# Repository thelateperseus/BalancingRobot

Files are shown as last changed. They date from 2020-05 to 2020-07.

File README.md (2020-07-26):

Balancing Robot Project
=======================

An Arduino-based, two-wheeled balancing robot.

Components:
* Arduino Nano
* MPU-6050 6 DoF sensor
* L298N motor driver
* Machifit 25GA370 DC 12V 130rpm Gear Reduction Motor with Mounting Bracket and Wheel
* 2x 4-AA battery holders with switch
* HC-06 bluetooth module for remote control (via Android app or hand-held remote control)

Control Algorithm
-----------------

The main control alorithm changes the motor speed based on the measured angle. If the robot tips forward or backward, the motors drive forward or backward to prevent the robot from falling over. Two PID controllers are used to achieve this. The first measures the angle from the MPU-6050 and changes the motor speed PWM signal. The second uses the motor speed PWM signal and changes the angle set point. The remote control sets the speed set point, and the PID controller adjusts the angle set point accordingly.

```
              Speed             Speed                   Angle             Angle                  Speed              Angle
-----------  setpoint  -------  error  --------------  setpoint  -------  error  --------------  output  ---------  reading
| Remote  | ---------> | Sum | ------> | Speed PID  | ---------> | Sum | ------> | Angle PID  | ---+---> | Robot | ---
| Control |          + -------         | Controller |          + -------         | Controller |    |     ---------   |
-----------               ^  -         --------------               ^  -         --------------    |                 |
                          |                                         |                              |                 |
                          |                                         -------------------------------+------------------
                          |                                                                        |
                          --------------------------------------------------------------------------
```

The motors do not have encoders, so the speed PWM signal is used as the actual speed of the robot. If the motors had encoders, we would read the actual speed from the encoders instead.

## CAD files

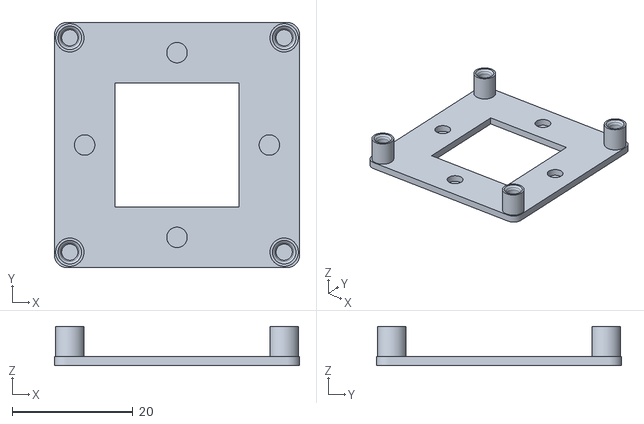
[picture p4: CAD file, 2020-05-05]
Solarbotics_L298_Compact_Motor_Driver_Mounting_Plate.stl
40.6 x 40.6 x 6.50

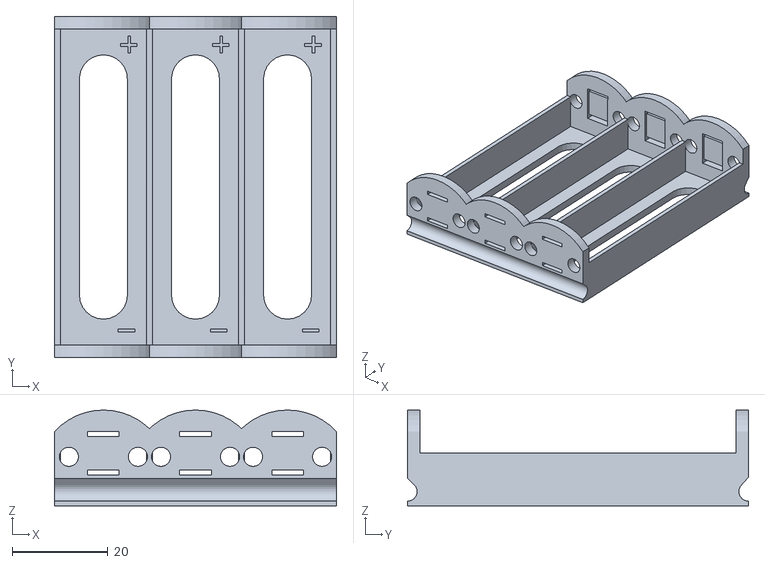
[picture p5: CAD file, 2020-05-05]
battaryholder3.stl
58.8 x 71.1 x 20.0

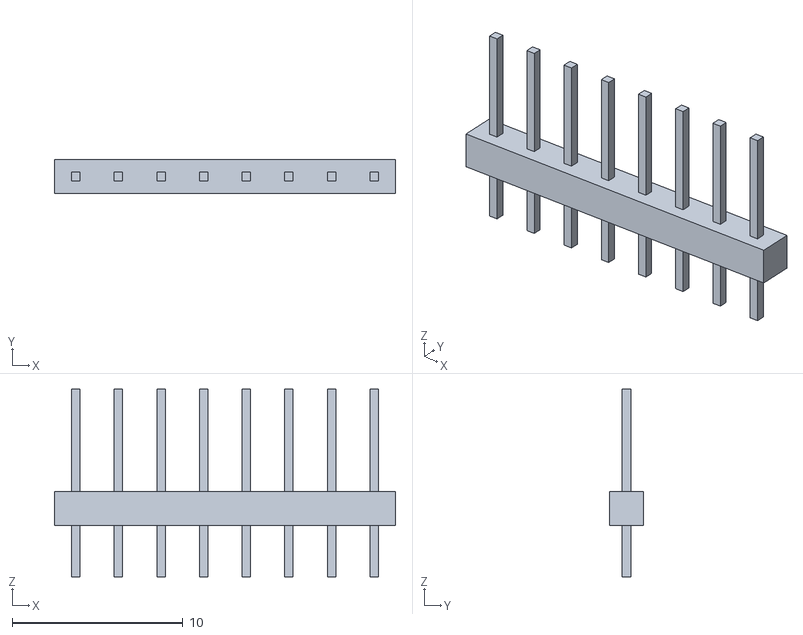
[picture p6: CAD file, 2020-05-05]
gy521_pins.stl
20.0 x 2.00 x 11.0

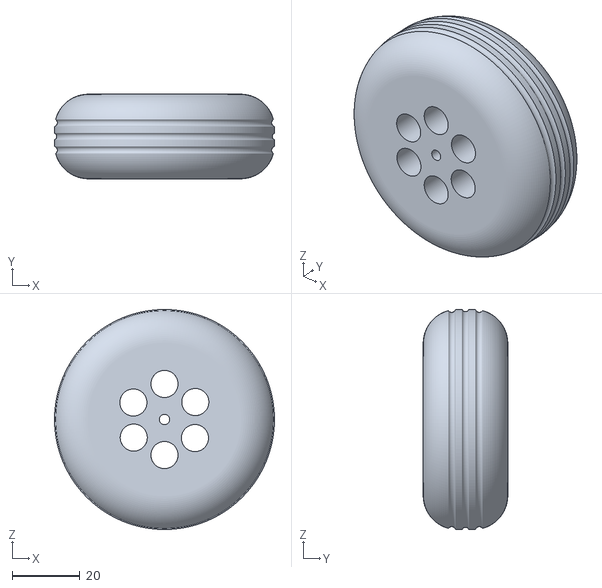
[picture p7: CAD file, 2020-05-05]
Wheel_65mm.stl
65.0 x 25.0 x 65.0

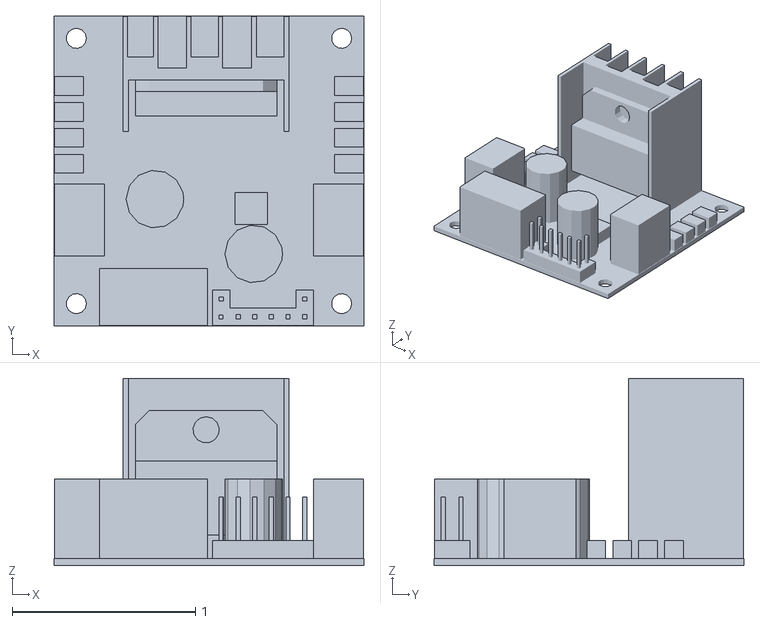
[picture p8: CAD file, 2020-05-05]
motor_driver.stl
1.69 x 1.69 x 1.02

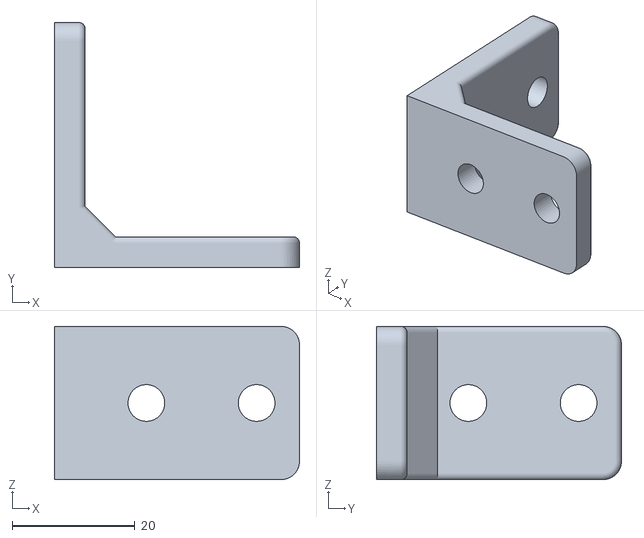
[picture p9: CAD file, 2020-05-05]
CornerBracket.stl
40.0 x 40.0 x 25.0

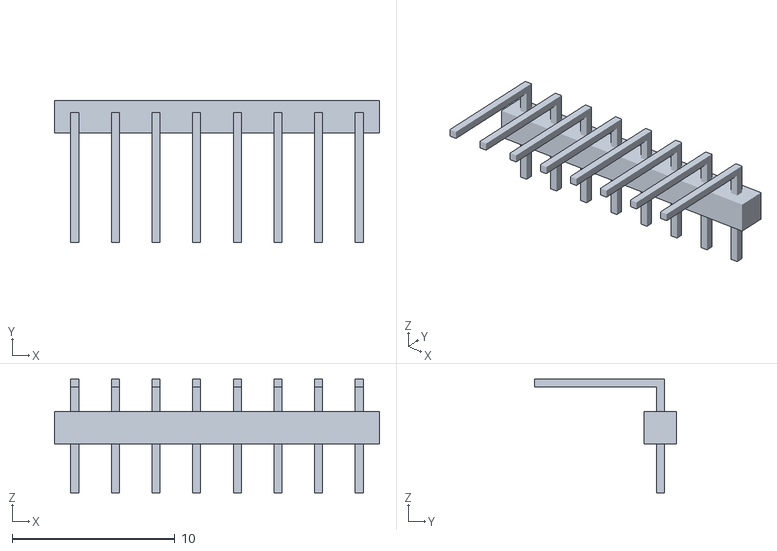
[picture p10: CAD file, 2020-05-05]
gy521_pins90deg.stl
20.0 x 8.75 x 7.00

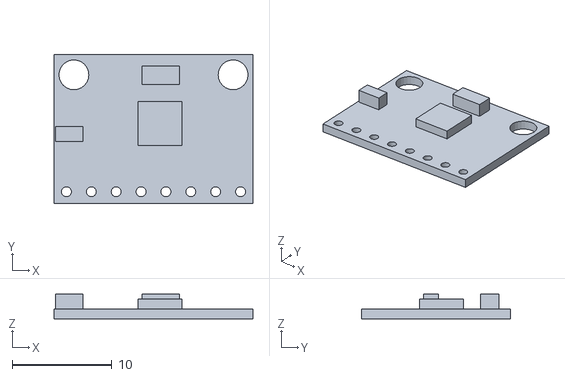
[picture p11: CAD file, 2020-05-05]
GY-521_MPU-6050.stl
20.0 x 15.0 x 2.50

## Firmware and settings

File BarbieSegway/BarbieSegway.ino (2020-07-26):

#include <Wire.h>
#include <PID_v1.h>
#include <SoftwareSerial.h>

const int IN1 = 7;
const int IN2 = 8;
const int ENA = 6;
const int IN3 = 9;
const int IN4 = 10;
const int ENB = 11;

const int GYRO_ADDRESS = 0x68;
const int ACCELEROMETER_Z_CALIBRATION = 300;
const int LOOP_MICROS = 4000;

boolean started = false;

long gyroXCalibration = 0, gyroYCalibration = 0;

double pitchSetPoint = 0;
double pitchReading = 0;
double pitchPidOutput = 0;
PID pitchPid(&pitchReading, &pitchPidOutput, &pitchSetPoint, 40, 140, 1, REVERSE);

double speedSetPoint = 0;
double filteredSpeed = 0;
double speedPidOutput = 0;
//PID speedPid(&pitchPidOutput, &speedPidOutput, &speedSetPoint, 0.00025, 0, 0.000005, DIRECT);
PID speedPid(&filteredSpeed, &speedPidOutput, &speedSetPoint, 0.00000008, 0.02 , 0, DIRECT);

double yawSetPoint = 0;
double yawReading = 0;
double yawOutput = 0;
PID yawPid(&yawReading, &yawOutput, &yawSetPoint, 1.5, 0, 0, DIRECT);

int activeCommand = -1;
unsigned long commandTimer = 0;

unsigned long loopEndTime = 0;

SoftwareSerial BTSerial(2, 3); // RX | TX

//Low pass butterworth filter order=1 alpha1=0.04
//http://www.schwietering.com/jayduino/filtuino/index.php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
class  LowPassFilter
{
  public:
    LowPassFilter() {
      v[0] = 0.0;
    }
  private:
    double v[2];
  public:
    double step(double x) { //class II
      v[0] = v[1];
      // 20Hz
      //v[1] = (2.043008243002644164e-1 * x)
      //   + (0.59139835139947116716 * v[0]);
      // 10Hz
      v[1] = (1.121602444751934047e-1 * x)
             + (0.77567951104961319064 * v[0]);
      return v[0] + v[1];
    }
};

LowPassFilter speedFilter = LowPassFilter();

void setup() {
  Serial.begin(115200);
  BTSerial.begin(38400);
  Serial.println("Initializing MPU-6050...");

  // Wake up the MPU-6050
  Wire.beginTransmission(GYRO_ADDRESS);
  Wire.write(0x6B); // PWR_MGMT_1 register
  Wire.write(0x00);
  Wire.endTransmission();
  // Set the full scale of the gyro to +/- 250 degrees per second
  Wire.beginTransmission(GYRO_ADDRESS);
  Wire.write(0x1B); // GYRO_CONFIG register
  Wire.write(0x00);                                                         //Set the register bits as 00000000 (250dps full scale)
  Wire.endTransmission();                                                   //End the transmission with the gyro
  // Set the full scale of the accelerometer to +/- 4g.
  Wire.beginTransmission(GYRO_ADDRESS);
  Wire.write(0x1C); // ACCEL_CONFIG register
  Wire.write(0x08);
  Wire.endTransmission();
  // Enable Digital Low Pass Filter to improve the raw data.
  Wire.beginTransmission(GYRO_ADDRESS);
  Wire.write(0x1A); // CONFIG register
  Wire.write(0x03); // ~43Hz
  Wire.endTransmission();

  Serial.println("Initializing L298N...");

  pinMode(IN1, OUTPUT);
  pinMode(IN2, OUTPUT);
  pinMode(ENA, OUTPUT);
  pinMode(IN3, OUTPUT);
  pinMode(IN4, OUTPUT);
  pinMode(ENB, OUTPUT);

  pitchPid.SetSampleTime(4);
  pitchPid.SetOutputLimits(-255, 255);
  speedPid.SetSampleTime(4);
  speedPid.SetOutputLimits(-15, 15);
  yawPid.SetSampleTime(4);
  yawPid.SetOutputLimits(-15, 15);

  Serial.println("Measuring gyro calibration values...");
  loopEndTime = micros() + LOOP_MICROS;
  for (int i = 0; i < 500; i++) {
    if (i % 15 == 0) {
      digitalWrite(LED_BUILTIN, !digitalRead(LED_BUILTIN));        //Change the state of the LED every 15 loops to make the LED blink fast
    }
    Wire.beginTransmission(GYRO_ADDRESS);
    Wire.write(0x43); // GYRO_XOUT[15:8]
    Wire.endTransmission();
    Wire.requestFrom(GYRO_ADDRESS, 4); // GYRO_XOUT[15:8], GYRO_XOUT[7:0], GYRO_YOUT[15:8], GYRO_YOUT[7:0]
    gyroXCalibration += Wire.read() << 8 | Wire.read();
    gyroYCalibration += Wire.read() << 8 | Wire.read();
    delayMicroseconds(loopEndTime - micros()); // Simulate the main program loop time
    loopEndTime = micros() + LOOP_MICROS;
  }
  // Get the average from the 500 readings
  gyroXCalibration /= 500;
  gyroYCalibration /= 500;

  /*Serial.print("Gyro calibration complete. x: ");
    Serial.print(gyroXCalibration);
    Serial.print(", y: ");
    Serial.println(gyroYCalibration);*/

  // x: -552, y: 66

  Serial.println("Ready to roll!");
  digitalWrite(LED_BUILTIN, HIGH);
  loopEndTime = micros() + LOOP_MICROS;
}

void loop() {
  // Remote control
  // --------------
  int command = -1;
  while (Serial.available()) {
    command = Serial.read(); //reads serial input
  }
  while (BTSerial.available()) {
    command = BTSerial.read(); //reads bluetooth input
  }
  if (command == 'l' || command == 'L') {
    yawSetPoint -= 2;
  } else if (command == 'r' || command == 'R') {
    yawSetPoint += 2;
  } else if (command == 'f' || command == 'F') {
    activeCommand = command;
    commandTimer = millis();
    speedSetPoint = 30;
  } else if (command == 'b' || command == 'B') {
    activeCommand = command;
    commandTimer = millis();
    speedSetPoint = -30;
  }

  unsigned long commandTimeMillis = millis() - commandTimer;
  if (commandTimer > 0 && commandTimeMillis > 150) {
    activeCommand = -1;
    commandTimer = 0;
    speedSetPoint = 0;
  }

  // Angle calculations
  // ------------------
  /* http://www.geekmomprojects.com/gyroscopes-and-accelerometers-on-a-chip/
     Filtered Angle = α × (Gyroscope Angle) + (1 − α) × (Accelerometer Angle)
     where
         α = τ/(τ + Δt)
         (Gyroscope Angle) = (Last Measured Filtered Angle) + ω×Δt
         Δt = sampling rate (4ms)
         τ = time constant greater than timescale of typical accelerometer noise (1s)
  */

  // Read z accelerometer value
  Wire.beginTransmission(GYRO_ADDRESS);
  Wire.write(0x3F); // ACCEL_ZOUT[15:8]
  Wire.endTransmission();
  Wire.requestFrom(GYRO_ADDRESS, 2); // ACCEL_ZOUT[15:8], ACCEL_ZOUT[7:0]
  long accelerometerZ = Wire.read() << 8 | Wire.read();
  accelerometerZ += ACCELEROMETER_Z_CALIBRATION;
  accelerometerZ = constrain(accelerometerZ, -8200, 8200);

  // Calculate the current pitch angle in degrees according to the accelerometer
  float pitchAccelerometer = asin((float)accelerometerZ / 8200.0) * 57.296;

  // Start balancing when angle is close to zero
  if (!started && pitchAccelerometer > -0.5 && pitchAccelerometer < 0.5) {
    pitchReading = pitchAccelerometer;
    started = true;
    pitchPid.SetMode(AUTOMATIC);
    speedPid.SetMode(AUTOMATIC);
    yawPid.SetMode(AUTOMATIC);
  }

  // Read X and Y gyro values
  Wire.beginTransmission(GYRO_ADDRESS);
  Wire.write(0x43); // GYRO_XOUT[15:8]
  Wire.endTransmission();
  Wire.requestFrom(GYRO_ADDRESS, 4); // GYRO_XOUT[15:8], GYRO_XOUT[7:0], GYRO_YOUT[15:8], GYRO_YOUT[7:0]
  long gyroX = Wire.read() << 8 | Wire.read();
  long gyroY = Wire.read() << 8 | Wire.read();

  gyroX -= gyroXCalibration;
  gyroY -= gyroYCalibration;

  // Calculate the angle in degrees traveled during this loop angle
  // (Gyroscope Angle) = (Last Measured Filtered Angle) + ω×Δt
  float pitchGyro = pitchReading + gyroY * 0.000031;

  // Complementary filter to combine the gyro and accelerometer angle
  // Filtered Angle = α × (Gyroscope Angle) + (1 − α) × (Accelerometer Angle)
  pitchReading = pitchGyro * 0.9996 + pitchAccelerometer * 0.0004;

  yawReading -= gyroX * 0.000031;

  if (started) {
    pitchSetPoint = speedPidOutput + 1; // imperfect placement of MPU6050
    pitchPid.Compute();

    //filteredSpeed = speedFilter.step(pitchPidOutput);
    filteredSpeed = pitchPidOutput;
    speedPid.Compute();

    yawPid.Compute();

    //Serial.print("yaw:");
    //Serial.print(yawReading);

    /*Serial.print("psp:");
      Serial.print(pitchSetPoint);
      Serial.print(", p:");
      Serial.print(pitchReading);*/
    Serial.print(", ssp:");
    Serial.print(speedSetPoint);
    Serial.print(", s:");
    Serial.print(pitchPidOutput);
    Serial.print(", fs:");
    Serial.print(filteredSpeed);
    Serial.println();

    /*
      // Deadband to prevent oscillations
      if (pitchPidOutput > 0 && pitchPidOutput < 2) {
      pitchPidOutput = 0;
      }
      if (pitchPidOutput < 0 && pitchPidOutput > -2) {
      pitchPidOutput = 0;
      }
    */

    double speedA = pitchPidOutput + yawOutput;
    double speedB = pitchPidOutput - yawOutput;
    if (pitchReading > 45 || pitchReading < -45 || pitchAccelerometer > 45 || pitchAccelerometer < -45) {
      speedA = 0;
      speedB = 0;
      pitchReading = 0;
      yawReading = 0;
      pitchSetPoint = 0;
      speedSetPoint = 0;
      yawSetPoint = 0;
      pitchPidOutput = 0;
      filteredSpeed = 0;
      speedPidOutput = 0;
      yawOutput = 0;
      activeCommand = -1;
      started = false;
      pitchPid.SetMode(MANUAL);
      speedPid.SetMode(MANUAL);
      yawPid.SetMode(MANUAL);
    }

    speedA = constrain(speedA, -255, 255);
    speedB = constrain(speedB, -255, 255);

    // control speed, deadzone A:50, B:40
    double pwmA = map(abs(speedA), 1, 255, 54, 255);
    double pwmB = map(abs(speedB), 1, 255, 40, 255);
    analogWrite(ENA, pwmA);
    analogWrite(ENB, pwmB);
    //control direction
    digitalWrite(IN1, speedA < 0 ? HIGH : LOW);
    digitalWrite(IN2, speedA > 0 ? HIGH : LOW);
    //direction reversed for second motor (wiring)
    digitalWrite(IN3, speedB < 0 ? LOW : HIGH);
    digitalWrite(IN4, speedB > 0 ? LOW : HIGH);
  }

  // The angle calculations are tuned for a loop time of 4 milliseconds
  delayMicroseconds(loopEndTime - micros()); // Simulate the main program loop time
  loopEndTime = micros() + LOOP_MICROS;
}

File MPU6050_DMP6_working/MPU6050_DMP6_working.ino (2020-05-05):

// I2C device class (I2Cdev) demonstration Arduino sketch for MPU6050 class using DMP (MotionApps v2.0)
// 6/21/2012 by Jeff Rowberg <jeff@rowberg.net>
// Updates should (hopefully) always be available at https://github.com/jrowberg/i2cdevlib
//
// Changelog:
//      2019-07-08 - Added Auto Calibration and offset generator
//		   - and altered FIFO retrieval sequence to avoid using blocking code
//      2016-04-18 - Eliminated a potential infinite loop
//      2013-05-08 - added seamless Fastwire support
//                 - added note about gyro calibration
//      2012-06-21 - added note about Arduino 1.0.1 + Leonardo compatibility error
//      2012-06-20 - improved FIFO overflow handling and simplified read process
//      2012-06-19 - completely rearranged DMP initialization code and simplification
//      2012-06-13 - pull gyro and accel data from FIFO packet instead of reading directly
//      2012-06-09 - fix broken FIFO read sequence and change interrupt detection to RISING
//      2012-06-05 - add gravity-compensated initial reference frame acceleration output
//                 - add 3D math helper file to DMP6 example sketch
//                 - add Euler output and Yaw/Pitch/Roll output formats
//      2012-06-04 - remove accel offset clearing for better results (thanks Sungon Lee)
//      2012-06-01 - fixed gyro sensitivity to be 2000 deg/sec instead of 250
//      2012-05-30 - basic DMP initialization working

/* ============================================
I2Cdev device library code is placed under the MIT license
Copyright (c) 2012 Jeff Rowberg

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
THE SOFTWARE IS PROVIDED "AS IS", WITHOUT WARRANTY OF ANY KIND, EXPRESS OR
IMPLIED, INCLUDING BUT NOT LIMITED TO THE WARRANTIES OF MERCHANTABILITY,
FITNESS FOR A PARTICULAR PURPOSE AND NONINFRINGEMENT. IN NO EVENT SHALL THE
AUTHORS OR COPYRIGHT HOLDERS BE LIABLE FOR ANY CLAIM, DAMAGES OR OTHER
LIABILITY, WHETHER IN AN ACTION OF CONTRACT, TORT OR OTHERWISE, ARISING FROM,
OUT OF OR IN CONNECTION WITH THE SOFTWARE OR THE USE OR OTHER DEALINGS IN
THE SOFTWARE.
===============================================
*/

// I2Cdev and MPU6050 must be installed as libraries, or else the .cpp/.h files
// for both classes must be in the include path of your project
#include "I2Cdev.h"

#include "MPU6050_6Axis_MotionApps20.h"
//#include "MPU6050.h" // not necessary if using MotionApps include file

// Arduino Wire library is required if I2Cdev I2CDEV_ARDUINO_WIRE implementation
// is used in I2Cdev.h
#if I2CDEV_IMPLEMENTATION == I2CDEV_ARDUINO_WIRE
    #include "Wire.h"
#endif

// class default I2C address is 0x68
// specific I2C addresses may be passed as a parameter here
// AD0 low = 0x68 (default for SparkFun breakout and InvenSense evaluation board)
// AD0 high = 0x69
MPU6050 mpu;
//MPU6050 mpu(0x69); // <-- use for AD0 high

/* =========================================================================
   NOTE: In addition to connection 3.3v, GND, SDA, and SCL, this sketch
   depends on the MPU-6050's INT pin being connected to the Arduino's
   external interrupt #0 pin. On the Arduino Uno and Mega 2560, this is
   digital I/O pin 2.
 * ========================================================================= */

/* =========================================================================
   NOTE: Arduino v1.0.1 with the Leonardo board generates a compile error
   when using Serial.write(buf, len). The Teapot output uses this method.
   The solution requires a modification to the Arduino USBAPI.h file, which
   is fortunately simple, but annoying. This will be fixed in the next IDE
   release. For more info, see these links:

   http://arduino.cc/forum/index.php/topic,109987.0.html
   http://code.google.com/p/arduino/issues/detail?id=958
 * ========================================================================= */



// uncomment "OUTPUT_READABLE_QUATERNION" if you want to see the actual
// quaternion components in a [w, x, y, z] format (not best for parsing
// on a remote host such as Processing or something though)
//#define OUTPUT_READABLE_QUATERNION

// uncomment "OUTPUT_READABLE_EULER" if you want to see Euler angles
// (in degrees) calculated from the quaternions coming from the FIFO.
// Note that Euler angles suffer from gimbal lock (for more info, see
// http://en.wikipedia.org/wiki/Gimbal_lock)
//#define OUTPUT_READABLE_EULER

// uncomment "OUTPUT_READABLE_YAWPITCHROLL" if you want to see the yaw/
// pitch/roll angles (in degrees) calculated from the quaternions coming
// from the FIFO. Note this also requires gravity vector calculations.
// Also note that yaw/pitch/roll angles suffer from gimbal lock (for
// more info, see: http://en.wikipedia.org/wiki/Gimbal_lock)
#define OUTPUT_READABLE_YAWPITCHROLL

// uncomment "OUTPUT_READABLE_REALACCEL" if you want to see acceleration
// components with gravity removed. This acceleration reference frame is
// not compensated for orientation, so +X is always +X according to the
// sensor, just without the effects of gravity. If you want acceleration
// compensated for orientation, us OUTPUT_READABLE_WORLDACCEL instead.
//#define OUTPUT_READABLE_REALACCEL

// uncomment "OUTPUT_READABLE_WORLDACCEL" if you want to see acceleration
// components with gravity removed and adjusted for the world frame of
// reference (yaw is relative to initial orientation, since no magnetometer
// is present in this case). Could be quite handy in some cases.
//#define OUTPUT_READABLE_WORLDACCEL

// uncomment "OUTPUT_TEAPOT" if you want output that matches the
// format used for the InvenSense teapot demo
//#define OUTPUT_TEAPOT



#define INTERRUPT_PIN 2  // use pin 2 on Arduino Uno & most boards
#define LED_PIN 13 // (Arduino is 13, Teensy is 11, Teensy++ is 6)
bool blinkState = false;

// MPU control/status vars
bool dmpReady = false;  // set true if DMP init was successful
uint8_t mpuIntStatus;   // holds actual interrupt status byte from MPU
uint8_t devStatus;      // return status after each device operation (0 = success, !0 = error)
uint16_t packetSize;    // expected DMP packet size (default is 42 bytes)
uint16_t fifoCount;     // count of all bytes currently in FIFO
uint8_t fifoBuffer[64]; // FIFO storage buffer

// orientation/motion vars
Quaternion q;           // [w, x, y, z]         quaternion container
VectorInt16 aa;         // [x, y, z]            accel sensor measurements
VectorInt16 aaReal;     // [x, y, z]            gravity-free accel sensor measurements
VectorInt16 aaWorld;    // [x, y, z]            world-frame accel sensor measurements
VectorFloat gravity;    // [x, y, z]            gravity vector
float euler[3];         // [psi, theta, phi]    Euler angle container
float ypr[3];           // [yaw, pitch, roll]   yaw/pitch/roll container and gravity vector

// packet structure for InvenSense teapot demo
uint8_t teapotPacket[14] = { '$', 0x02, 0,0, 0,0, 0,0, 0,0, 0x00, 0x00, '\r', '\n' };
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

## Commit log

2020-05-05 Initial commit
    Basic PID control for motors based on accelerometer data only. Deadband
    compensation for motors to try to match their speeds.
    Also includes a test program to find the motor deadband, and a test
    program to use the DMP on the MPU6050 to calculate pitch and roll
    angles.
    [CornerBracket.stl, GY-521_MPU-6050.stl, Solarbotics_L298_Compact_Motor_Driver_Mounting_Plate.stl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]
2020-05-05 Basic balancing using I2Cdev library with ypr
    Added I2Cdev library and tuned PID constants to achieve basic balancing.
    Robot can balance for a minute or so, but this depends on being placed
    on a stand on power-up to determine the pitch angle setpoint (since the
    returned pitch is relative to the position on power-up).
    Sometimes the robot seems to slowly oscillate and eventually fall over.
    Further tuning of the PID parameters (and maybe sample time) will
    hopefully rectify this.
    Also further tuned dead band parameters for the motors. However, the
    motors still move a little independently when moving at slow speeds.
    [BalanceRobot.ino]
2020-05-06 Increased PID gains for stability
    [BalanceRobot.ino]
2020-05-07 Added yaw PID control
    Prior to this, the robot would tend to change heading as the wheels
    sometimes move independently. This additional PID control causes the
    robot to recenter to its original heading.
2020-05-07 Added basic RC functions
    Turn left or right by adjusting the yaw setpoint. Move forward or
    backward by changing the pitch setpoint. Forward/backward driving is not
    very reliable and the robot often wanders back to the point it started
    from after moving.
    Still todo:
    * handle wrap-around for yaw from -180 to 180
    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
2020-05-14 Replaced I2Cdev code with direct MPU-6050 comms
    Adapted code from [Your Arduino Balancing Robot (YABR)](http://www.brokking.net/yabr_main.html) to read accelerometer and gyro values directly from the MPU-6050 and combine them with a complementary filter. This allows the MPU-6050 to be mounted vertically so I can plug it directly into my breadboard (rather than attach with Blu-Tac and have jumper cables). The old I2Cdev code could not calculate the YPR angles in this orientation (presumably due to gimble lock). Also, the new code should allow easier control of the yaw angle because I won't have to worry about wrap-around from 180 to -180 degrees.
    Basic testing of the code is complete (i.e. t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
    [BalanceRobot.ino]
2020-05-15 Balancing improvements - PID, balance point
    Altered PID constants for faster control loop (4ms vs 5ms) and fresh batteries (1.6v AA alkaline). All gains are lower than previous iteration.
    Also implemented a balance setpoint adjustment which changes the pitch setpoint to try to stop the robot wandering. If the robot is not stationary, change the setpoint to try to make it stationary.
    Added a deadband to stop small motor movements when the robot is balanced.
    Robot seems more stable than before and does not move around as much.
2020-05-16 Basic forwards and backwards driving
    Accept a command over serial that lasts for 5 seconds. F changes the pitch setpoint to a small positive value, and B changes it to a small negative value. Monitor the output of the PID controller and adjust the setpoint to ensure that the motors are moving, but try to prevent them moving too fast (which would make the robot fall over).
    Also increased PID gain Kd to reduce oscillations from dynamic disturbance.
    [BalanceRobot.ino]
2020-05-16 Improved speed control with PID controller
    Added a second PID controller which measures speed and controls the pitch angle setpoint. This replaces both the previous balance setpoint code and the drive setpoint code. Now the remote command simply sets a target speed and the PID controller changes the pitch angle setpoint to achieve that speed.
    Further tuning of this PID controller is required, as is some filtering of the speed value to reduce noise.
    [BalanceRobot.ino]
2020-05-19 Added low-pass filter on speed signal
    The speed sent to the motors is quite noisy, so added a 20Hz low pass filter to the signal before it's fed into the PID controller to determine the angle set point.
2020-05-19 Yaw measurement and control
    Added yaw measurement and control. Prior to this, the robot would drift left or right due to the motors not engaging with a consistent deadband. Measuring yaw also allows for steering by setting the yaw setpoint.
    [BalanceRobot.ino]
2020-06-15 Initial remote control app
    Android app to connect to the robot via bluetooth and shows a button to drive the robot forwards.
2020-06-16 Back, Left and Right remote functions
    Added buttons for back, left and right movements of the robot.
2020-06-20 Change remote control to hold buttons
    Previous remote control would move the robot forward for 5 seconds when the button was pressed. This version changes the app to send the currently pressed button every 100 milliseconds. It also chang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
2020-06-28 Adjusted PID controller gains for Barbie
    Added Barbie to the top of the robot and adjusted the PID controller gains to account for the new centre of mass.
2020-06-28 Improved stability
    Converted speed controller from a PD controller where the output was added to the pitch setpoint, to a PI controller which sets the pitch setpoint directly (with a fudge factor because the MPU6050 is not exactly vertical on the breadboard.
    [BarbieSegway.ino]
2020-07-06 New remote control using analogue joystick
    I built a remote control using an Arduino Nano, an analogue joystick and an HC-05 bluetooth module. The HC-05 seems to have a buffering mechanism which stores characters in a 230 byte buffer. It tran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
2020-07-26 Adjusted constants for soldered circuit board
    Moved the robot controller from a breadboard to a soldered perfboard PCB and adjusted constants accordingly. The MPU-6050 breakout board is now soldered directly to the PCB to keep it steady. The spe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
    Also moved the joystick remote from a breadboard to a soldered perfboard PCB, and adjusted the joystick orientation accordingly.
